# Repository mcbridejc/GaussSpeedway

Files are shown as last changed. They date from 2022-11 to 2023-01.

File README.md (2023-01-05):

Gauss Speedway
==============

PCB design for the [Gauss Speedway](https://jeffmcbride.net/gauss-speedway/). Designed in Kicad 6.

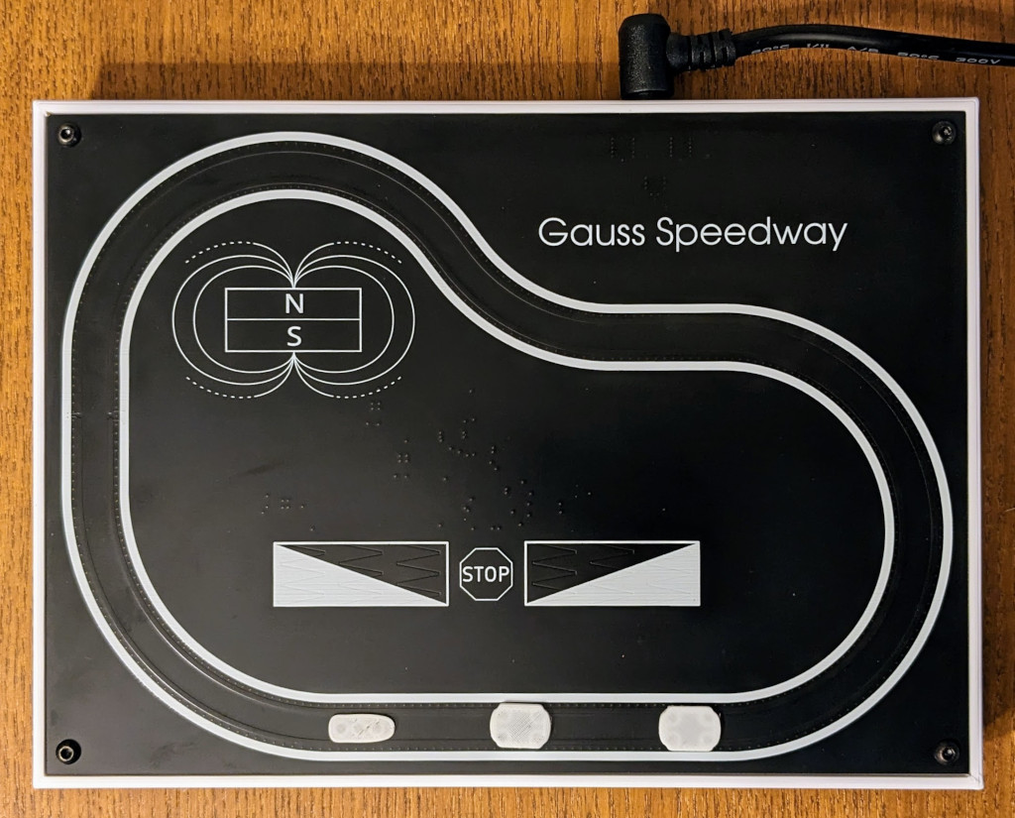
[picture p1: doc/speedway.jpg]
Gauss Speedway


Demo video: [https://vimeo.com/771275219](https://vimeo.com/771275219)

Firmware: [https://github.com/mcbridejc/speedway-controller](https://github.com/mcbridejc/speedway-controller)

# PCB

The board is a 4-layer board. I typically order it in black soldermask, although this is of course not necessary. I also typically do 1oz inner copper (thinner copper is typically the default) in order to get the trace resistance down. 

# Assembly

The holes in the corners are designed to accomodate M3 screws for mounting. The PCB mounts into a [3D printable frame](./doc/GaussSpeedway_Frame.stl), which has holes to accomodate M3 threaded heat inserts. You can also get by just putting four stand-offs on the corners.

## Cars

The cars can be printed on an FDM printer. I typically use a small 0.2mm nozzle for finer features. You may need to make some adjustments for your printer, the holes for the magnet can be tricky. Ideally, you have enough of a friction fit that the magnets will stay in place while the glue sets, but enough clearance that you can get them in easily. I typically insert them by placing the magnet on the end of a small flat head screw driver, placing a drop of medium CA into the hole, and then press-fit the magnet into the hole. You have to take care to place the magnets in the correct direction.

There are STL files for two car designs in this repo. [This one](./doc/MagnetCar202211.stl) is the better one, with four magnets spaced properly for the guard rails. Just to show some variety, I also put up a [narrow car](./doc/SkinnyCar.stl) with a single row of three magnets. It works as well, all though it is a bit more prone to flying off the track at high velocity.

You can also design your own cars. You just need to maintain the magnet spacing so that all magnets are on the same current direction. It's also pretty important to keep them light; the force created here is pretty small, and if they get too heavy they may just not move, or they may have a harder time staying on the track around a curve. 

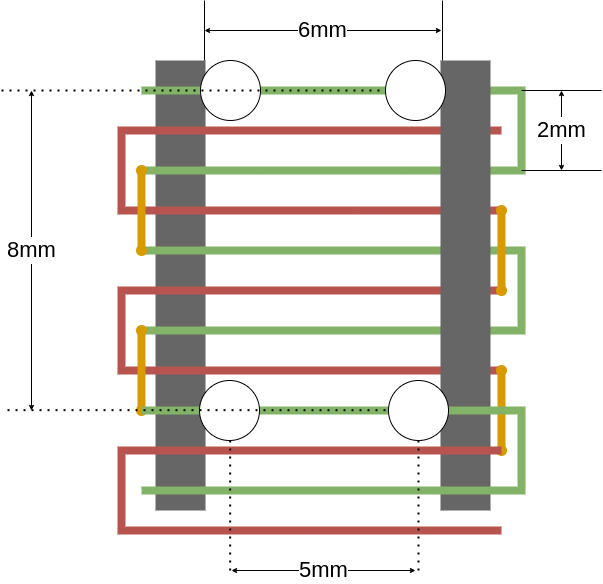
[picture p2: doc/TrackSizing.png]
Magnet Sizing


# Status 

Rev 3 is tested and seems to be correct.

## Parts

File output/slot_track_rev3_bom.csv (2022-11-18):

Reference | Value | Footprint | Mfg Part Number | Quantity Per PCB | LCSC | JLCPCB Part # | Comment | Config | Alternates
C1,C4,C5,C7 | 0.22uF | C_0603_1608Metric | CL10B224KA8NNNC | 4 | C21120 | C21120 | CAP CER 0.22UF 25V X7R 0603
C2,C3,C6,C8,C9,C10 | 10uF | C_0805_2012Metric | CL21A106KAYNNNG | 6 | C15850 | C15850 | CAP CER 10UF 25V X5R 0805
C11,C12,C13,C14 | 47nF | C_0603_1608Metric | CL10B473KB8WPNC | 4 | C1622 | C1622 | CAP CER 0.047UF 50V X7R 0603
J1 | Barrel_Jack_Switch | RASM722BK_Barrel | RASM722BK | 1 |  |  | CONN PWR JACK 2X5.5MM SOLDER
J2 | JST PH | JST_PH_S8B-PH-SM4-TB_1x08-1MP_P2.00mm_Horizontal | S8B-PH-SM4-TB(LF)(SN) | 1 | C265121 | C265121 | CONN HEADER SMD R/A 8POS 2MM
L1,L2,L3 | 68u | L_Bourns_SRR1260 | SRR1260A-680M | 3 |  |  | FIXED IND 68UH 2.1A 110 MOHM SMD
R1,R2,R3,R4,R5,R6,R7,R8,R9,R10,R11,R12 | 1k | R_0603_1608Metric | AC0603JR-101KL | 12 | 0603WAF3001T5E | 0603WAF3001T5E | RES 1k 0603 +/- 5% 0.1W Thick Film
U2 | MCP1754S-3302xCB | SOT-23 | TPMCP1703T-3302E/CB | 1 | C3040638 | C3040638 | IC REG LIN 3.3V 150MA SOT23A-3 |  | MCP1754ST-3302E/CB,TPMCP1703T-3302E/CB
U1 | STM32F051C6Tx | LQFP-48_7x7mm_P0.5mm | STM32F051C8T6 | 1 | C9863 | C9863 | IC MCU 32BIT 32KB FLASH 48LQFP
U3,U4,U5 | ZXBM5210-SP | Diodes_SO-8EP | ZXBM5210-SP-13 | 3 | C460767 | C460767 | IC MOTOR DRIVER 3V-18V 8SO

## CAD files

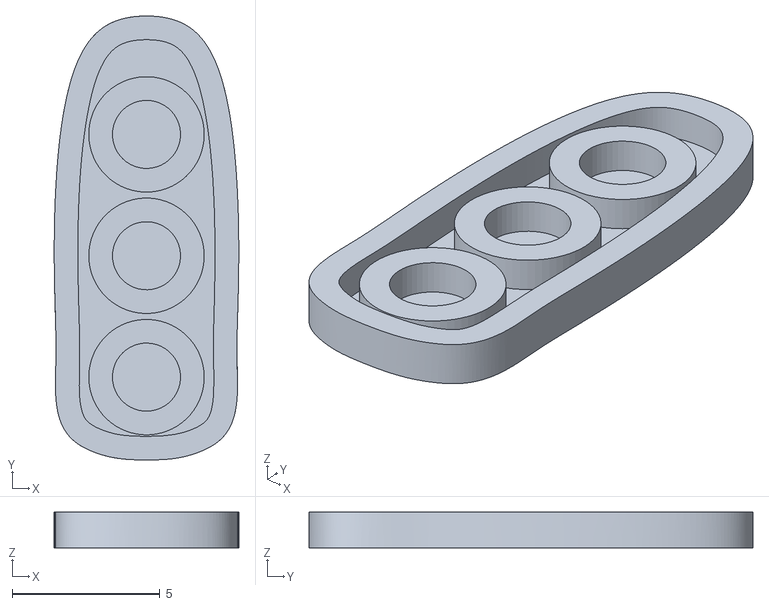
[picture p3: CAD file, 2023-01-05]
doc/SkinnyCar.stl
6.24 x 15.0 x 1.20

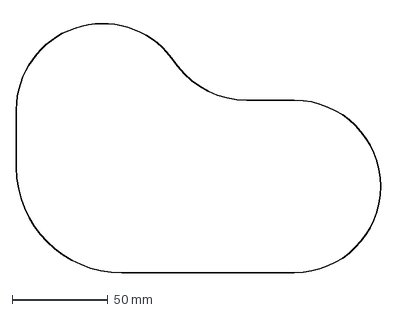
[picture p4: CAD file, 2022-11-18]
track.dxf
190.0 x 133.8 mm

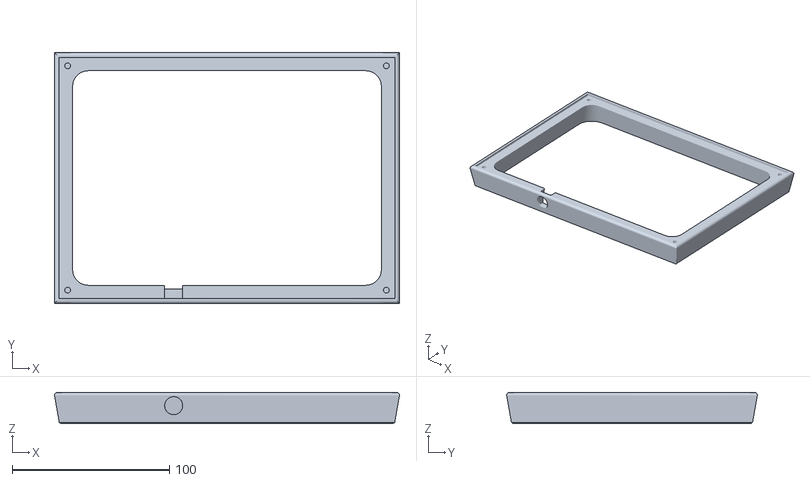
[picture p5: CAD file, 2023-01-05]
doc/GaussSpeedway_Frame.stl
219.2 x 159.3 x 20.0

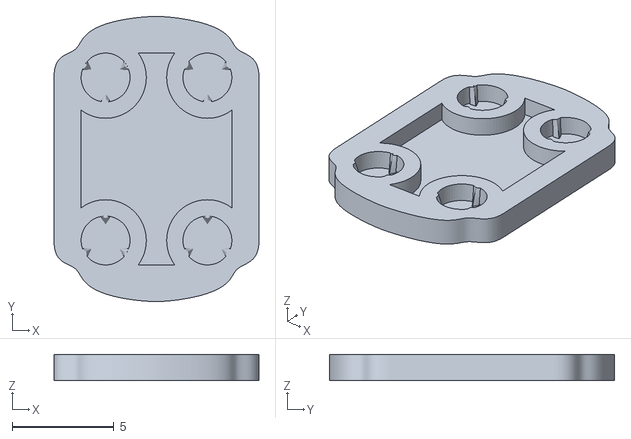
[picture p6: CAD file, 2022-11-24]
doc/MagnetCar202211.stl
10.1 x 14.0 x 1.30

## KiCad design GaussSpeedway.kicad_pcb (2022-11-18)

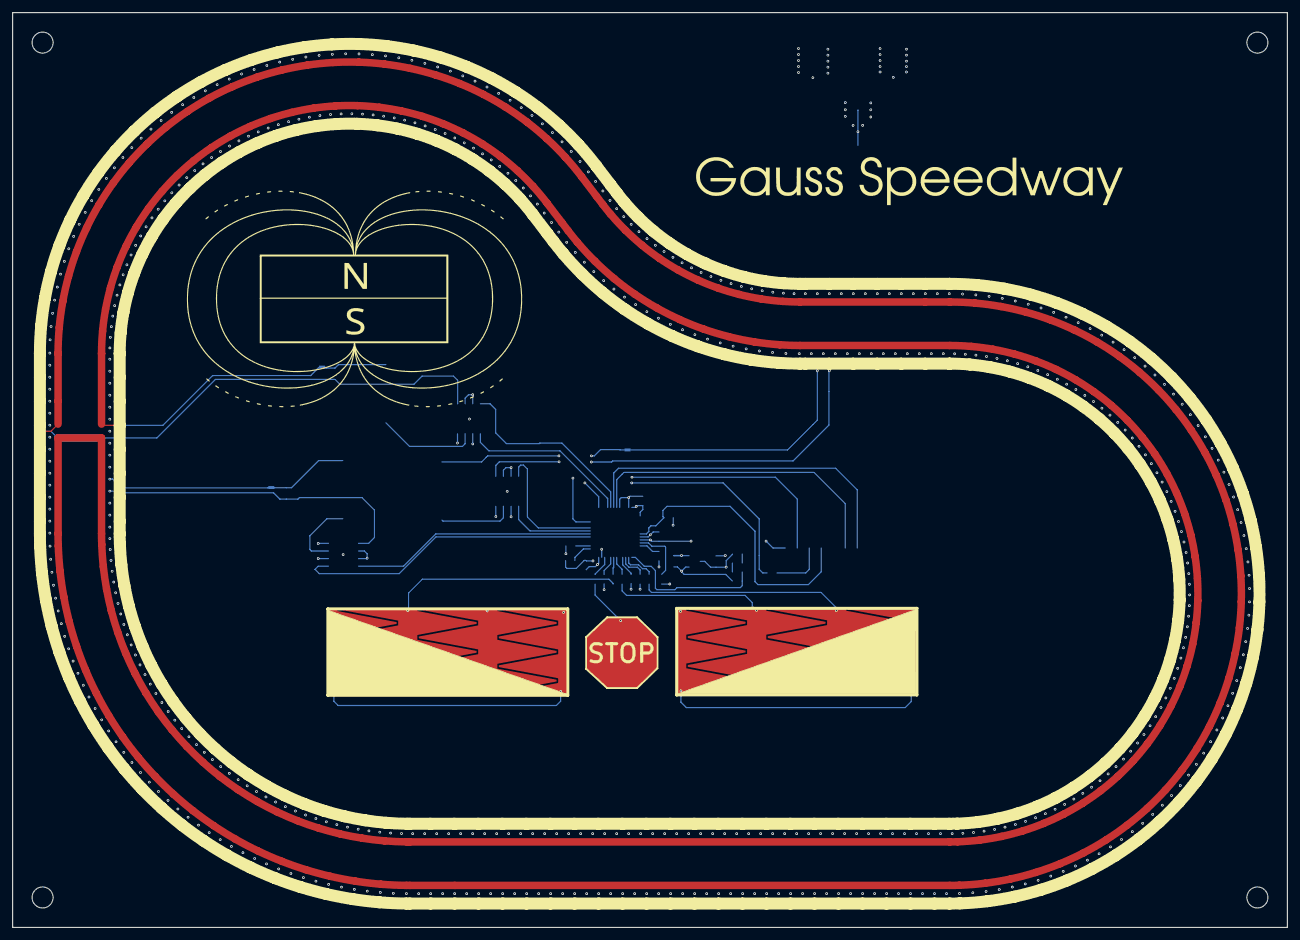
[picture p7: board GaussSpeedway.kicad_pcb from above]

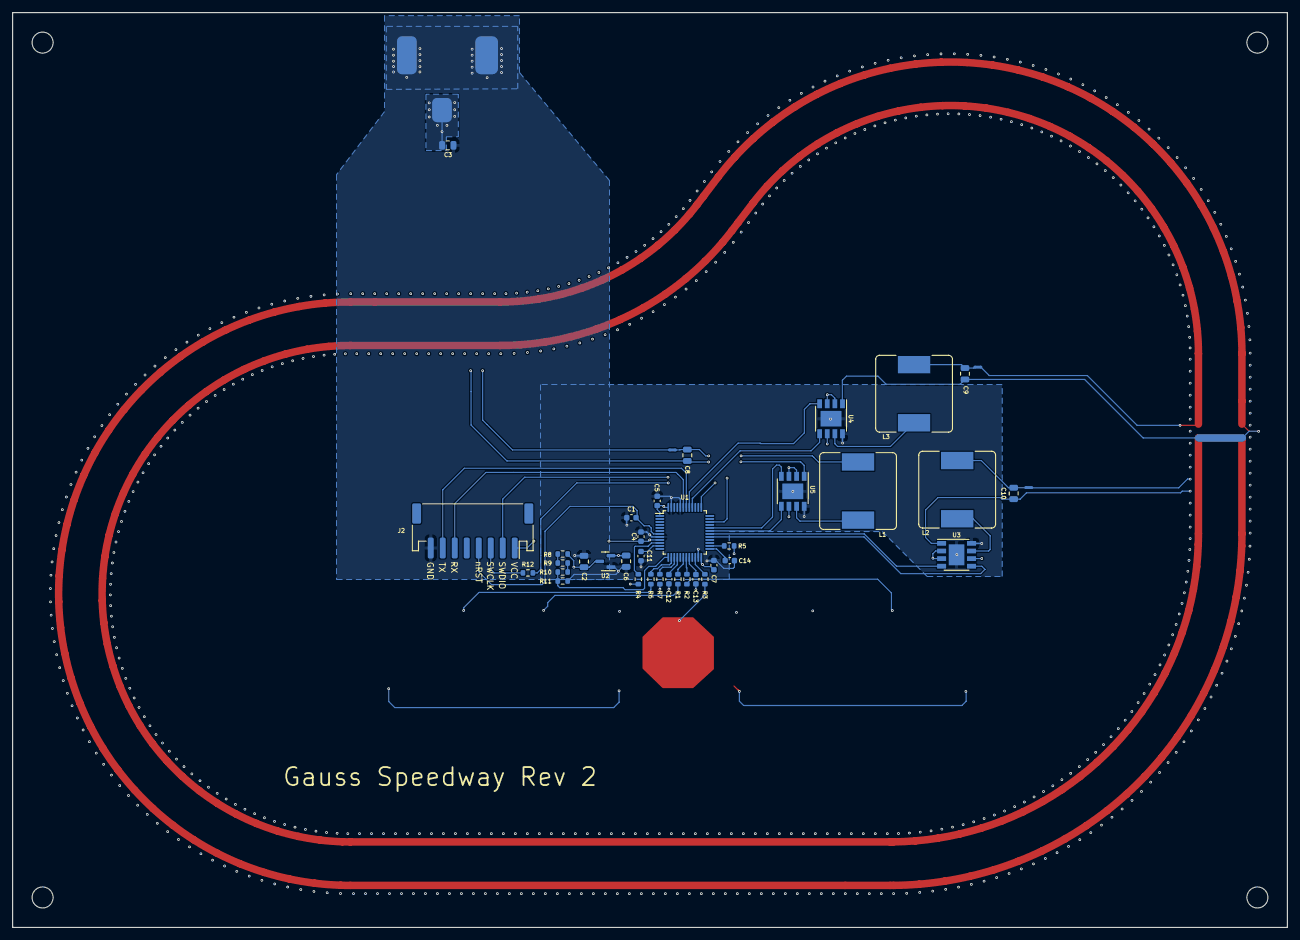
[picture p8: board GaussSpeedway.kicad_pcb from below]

Board: 4 copper layers, 212.5 x 152.5 mm, 47 parts (39 on the bottom side), 45 nets.

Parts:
C1, C4, C5, C7: 0.22uF; C_0603_1608Metric
C2, C3, C6, C8, C9, C10: 10uF; C_0805_2012Metric
C11, C12, C13, C14: 47nF; C_0603_1608Metric
G1: Graphic; magnetlogo
H1, H2, H3, H4: MountingHole; MountingHole_3.5mm
J1: Barrel_Jack_Switch; RASM722BK_Barrel
J2: JST PH; JST_PH_S8B-PH-SM4-TB_1x08-1MP_P2.00mm_Horizontal
L1, L2, L3: 68u; L_Bourns_SRR1260
NT1, NT2, NT5: NetTie_2; NetTie-2_SMD_Pad0.5mm
R1, R2, R3, R4, R5, R6, R7, R8, R9, R10, R11, R12: 1k; R_0603_1608Metric
T1, T3: LinearTouch4; linear_touch_40.0mm
T2: Conn_01x01; button
U1: STM32F051C6Tx; LQFP-48_7x7mm_P0.5mm
U2: MCP1754S-3302xCB; SOT-23
U3, U4, U5: ZXBM5210-SP; Diodes_SO-8EP

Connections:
/1A_N: L1.1, U5.7 (OUT2)
/1A_P: C8.1, NT1.2, U5.1 (OUT1)
/1B_N: L2.1, U3.7 (OUT2)
/1B_P: C10.1, NT2.2, U3.1 (OUT1)
/A_IN1: U1.32 (PA11), U5.4 (FWD)
/A_IN2: U1.31 (PA10), U5.5 (REV)
/B_IN1: U1.30 (PA9), U3.4 (FWD)
/B_IN2: U1.29 (PA8), U3.5 (REV)
/FWD1: R5.2, T1.1, T1.4
/FWD2: R7.2, T1.2
/FWD3: R2.1, T1.3
/G1_N: L3.1, U4.7 (OUT2)
/G1_P: C9.1, NT5.2, U4.1 (OUT1)
/G1_SAMPLE: C11.1, U1.11 (PA1)
/G2_SAMPLE: C12.1, U1.16 (PA6)
/G3_SAMPLE: C13.1, U1.20 (PB2)
/G6_SAMPLE: C14.1, U1.25 (PB12)
/G_IN1: U1.41 (PB5), U4.4 (FWD)
/G_IN2: U1.40 (PB4), U4.5 (REV)
/NRST: C1.2, J2.4, U1.7 (NRST)
/REV1: R4.2, T3.1, T3.4
/REV2: R6.2, T3.2
/REV3: R1.1, T3.3
/STOP: R3.1, T2.1
/SWCLK: J2.3, R12.1
/SWDIO: J2.2, U1.34 (PA13)
/UART_RX: J2.6, U1.43 (PB7)
/UART_TX: J2.7, U1.42 (PB6)
/VBUS_SENSE: R10.1, R11.2, U1.13 (PA3)
GND: C1.1, C2.2, C3.2, C4.1, C5.1, C6.2, C7.2, C11.2, C12.2, C13.2, C14.2, J1.2, J1.3, J2.8, R11.1, U1.8 (VSSA), U1.23 (VSS), U1.44 (BOOT0), U1.47 (VSS), U2.1 (GND), U3.8 (GND), U3.9 (GND), U4.8 (GND), U4.9 (GND), U5.8 (GND), U5.9 (GND)
unnamed: C8.2, L1.2, NT1.1
unnamed: C9.2, L3.2, NT5.1
unnamed: C10.2, L2.2, NT2.1
unnamed: R1.2, U1.18 (PB0)
unnamed: R2.2, U1.19 (PB1)
unnamed: R3.2, U1.22 (PB11)
unnamed: R4.1, U1.10 (PA0)
unnamed: R5.1, U1.26 (PB13)
unnamed: R6.1, U1.14 (PA4)
unnamed: R7.1, U1.15 (PA5)
unnamed: R8.1, R9.2
unnamed: R9.1, R10.2
unnamed: R12.2, U1.37 (PA14)
VBUS: C2.1, C3.1, J1.1, R8.2, U2.3 (VI), U3.2 (VM), U3.3 (VDD), U3.6 (VREF), U4.2 (VM), U4.3 (VDD), U4.6 (VREF), U5.2 (VM), U5.3 (VDD), U5.6 (VREF)
VCC: C4.2, C5.2, C6.1, C7.1, J2.1, U1.1 (VBAT), U1.9 (VDDA), U1.24 (VDD), U1.48 (VDD), U2.2 (VO)

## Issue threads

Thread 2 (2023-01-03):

known rev2 issues

ain101, 2023-01-03:
Ground planes not connected.

I managed to get a single 2mm magnet go round after fixing the ground.
Are there any additional known issues?

mcbridejc, 2023-01-04:
Yes, disconnected planes was the big issue. Rev 3 will be released soon; I have the first assembled. The other changes are:

1) the guard rail cross bar (connecting inner and outer traces) is moved to In2 layer, because the guard current interferes too much on the top layer.
2) Larger phase traces to lower resistance
3) Better heat dissipation from drivers so they don't get so warm.

Closed 2023-01-04.

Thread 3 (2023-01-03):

car measurements

ain101, 2023-01-03:
Can I have measurements of the car?
Only thing I found is [https://jeffmcbride.net/assets/images/cars-236b3de125109f96dcf6549c82793b25.jpg](https://jeffmcbride.net/assets/images/cars-236b3de125109f96dcf6549c82793b25.jpg)

mcbridejc, 2023-01-04:
Yes! I am soon doing a better release with rev3 of the board, and I know I need to put out some car STLs as well. But the magnet center-to-center spacing is 8mm in the along-track direction, and 5mm across.

Closed 2023-01-04.

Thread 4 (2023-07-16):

Suggested PCB fab?

adamcritchley, 2023-07-16:
I did a run with v3 of the board with 1oz inner and outer layers but I'm having issues with the velocity touch buttons. If the velocity is hardcoded then it works with a single magnet but not accurate enough to keep the entire car on the track. I'm thinking it may have been the fab I used.

Do you have a recommended PCB fab?

mcbridejc, 2023-07-16:
Hi! I used JLCPCB for mine, but I don't really think it should matter much where you get it built.

### Capacitive touch

 I'm not sure what sort of problems you're seeing, but I wonder if the calibration I did might not work well enough for your boards. Although I hoped it was primarily a function of the trace geometry and that it would be consistent across batches, I don't know if it is (it seemed to be consistent within my batch of boards, at least). I determined the calibration by pushing the raw capacitance measurements out the serial port, and capturing them while sliding a finger across the sliders. Then I just computed scale factors to "normalize" them, so the maximum values were consistent. If you're up for some data collection, and able to read to the serial port on the debug connector, I could send you a firmware for it.

### Keeping cars on the track

There could be a lot going on here; and there are always some operating conditions where a car will fly off the track -- e.g. if you go too fast. Is what you're seeing that the cars move but go straight off the track when it hits a curve? The main batch-to-batch variation I would expect to matter is trace resistance. Since the software just controls duty cycle and it can't measure the actual current, if the resistance changes so will the currents. Are you able to measure the trace resistances? On mine, the phases are about 5 ohms, and the guard rails are 0.8 ohms, and this is codified [here](https://github.com/mcbridejc/speedway-controller/blob/main/app/src/main.rs#L82) (note the 1.4 ohm extra is accounting for the resistance of the FETs).

adamcritchley, 2023-07-16:
We used JLPCB as well. I can absolutely collect those slider measurements. How would I get that firmware from you?

The cars kind of slowly and gently meander off the side of the track. A single magnet works pretty well but not the entire car. I'll reply with those trace resistance measurements tomorrow. Thanks!

mcbridejc, 2023-07-16:
Any chance the car magnets are installed backwards? They all need to be
aligned, and also there is a "right" polarity based on the gaurd rail
current direction.

The other thing to check: validate the guard rail current. Find the
capacitor across the guard traces, get the resistance on it while powered
off and then measure the voltage across it while powered on.

Oh, and since it sounds like you modified the software to bypass the touch
control, I guess just make sure that you modified it in such a way that the
guard rail  is still turned on.

On Sun, Jul 16, 2023, 2:15 PM Adam Critchley ***@***.***>
wrote:

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

adamringer, 2023-07-16:
Are the magnets all supposed to be installed with the same polarity,  or is one side supposed to have opposite polarity from the other side?  Right now we have them installed all with the same polarity.

mcbridejc, 2023-07-16:
All with the same polarity, and it cant be arbitrary. One polarity is wrong
and if backwards it will move but the guard rails will not contain the car,
but rather will be unstable and tend to push it off the track. Switching
the direction of the guard rail current has the same effect as flipping the
magnets around.

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

adamcritchley, 2023-07-18:
Good news! The capacitive touch buttons work at least some of the time.

How would I collect trace measurements from the track? I thought the edges of the tracks were VIAs that I could access with the multimeter probe but they seem to be capped.

adamcritchley, 2023-07-23:
Thanks for the measurement directions! I'll have them to you shortly.

adamcritchley, 2023-08-01:
Is C10 the guard rail capacitor? I get 5.5 ohms powered off. And voltage is 2.5 to 2.9 powered on. For C9, I get 0.6 ohms and 0.5v

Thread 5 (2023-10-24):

Using MCT Stepper Motor driver instead?

beniroquai, 2023-10-24:
Hey @mcbridejc, this project is amazing! Thank you so much for making it open-source and providing such nice documentation!
I'm a little lazy and was wondering if - instead of the electronics in the current version - I could simply use a TMC stepper driver. What would be the drawback here? I can imagine that micro stepping would allow me to have a more precise motion. i was thinking of building a small xy microscope stage based on this design.
Do you have a rough estimate on the force that is available for pulling stuff over a surface? Or in other terms, what's the maximum load of the small "car" can carry in your track setup?

mcbridejc, 2023-10-26:
Thanks @beniroquai!

You can definitely use stepper drivers -- in fact that's what I used on the first prototype. The only concern that pops into my head is making sure you have enough inductance for the driver. I think some of them expect/require considerable current. I ended up adding 68uH inductors to keep the ripple down.

I am doing  microstepping (8X, 16X? I forget exactly, but some amount) in the code on the controller. I don't think it make a huge difference, to be honest.

I don't have a very quantitative estimate, but the force is quite low. The cars are printed quite thin, and if they get perhaps 2 or 3X as heavy I think they won't move reliably (with the same magnets anyway). I tried to weight a car, but my scale seems to have lost its calibration and I seem to have lost my calibration weights at the moment.

For precise positioning, the friction is usually too high. I can't move the car back and forth within a step period reliably at all. I have seen people use paramagnetic films to get some lifting force and either lower the friction or even levitate a bit, so that's something to consider...but I can say if you tried to move a 75mm microscope slide with my setup it's not even close to working -- although there's nothing to say you can't get bigger magnets and more current!

beniroquai, 2023-10-27:
Thanks for the detailed response!

I feared the lack of force to move a sample eventually. After doing some research I also found some projects that could move a magnet in [XY](https://hackaday.io/project/154496-2d-actuator-move-micro-robot-in-xy-2d-space ). It could even move smaller parts like LEGO pieces, so this sparked the idea of having an ultra low-cost and perfectly planar XY stage for scanning blood smears to detect malaria parasites eventually. Here, price matters :)
The current prototype looks like this and I can imagine that the XY stage can be replaced (if you are curious: [UC2](http://openuc2.github.io/)):
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

Regarding "more current", I found this implementation https://benwang.dev/2022/08/09/PCB-Linear-Actuator.html. He uses a 3 phase synchronous motor. Pretty cool, but I'm lacking the knowledge to get this to work eventually. I'm also more familiar with ESP's than STMs ;)
But perhaps I have to go for the "bigger is better" path. I'll order some PCBs generated with your beautiful scripts to get a feeling for their performance. If you're keen to support this crazy idea, perhaps we could have a chat :)

Thanks a lot again!

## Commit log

2022-11-04 Rev 1 as ordered
    [slot_track-B_Cu.gbr, slot_track-B_Mask.gbr, slot_track-B_Paste.gbr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]
2022-11-18 Rev 2
    - Adjusts track shape
    - Swaps guard rails to top and phase to In1. Hopefully this lowers the
    noise and friction.
    - Adds sample caps
    - Adds SWCLK resistor
    - Adds divider for Vin measurement
    - Switches to a PH connector for SWD and a UART
    [slot_track-B_Cu.gbr, slot_track-B_Mask.gbr, slot_track-B_Paste.gbr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]
2022-11-24 Add readme, STL and image
    [MagnetCar202211.stl]
2022-11-24 Rename project files
    [GaussSpeedway.kicad_pcb, GaussSpeedway.kicad_sch]
2023-01-05 Revert an accidental eeschema nightly infection
    [GaussSpeedway.kicad_sch]
2023-01-05 Updates for rev 3
    - Expand planes and add vias under hbridge drivers for better thermal
    dissipation
    - Add some thermal dissipation planes on inductor pads
    - Move guard rail current crossover to In2, further from cars and
    closer to the balanced return current on the bottom layer
    - Increase drive trace width from 0.3 to 0.45mm
    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
    [GaussSpeedway-B_Cu.gbr, GaussSpeedway-B_Mask.gbr, GaussSpeedway-B_Paste.gbr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]
2023-01-05 Add STLs and update README
    [GaussSpeedway_Frame.stl, SkinnyCar.stl]
2023-01-05 Add notes about 1oz inner copper on PCB
2023-01-05 Replace image with black soldermask rev3
